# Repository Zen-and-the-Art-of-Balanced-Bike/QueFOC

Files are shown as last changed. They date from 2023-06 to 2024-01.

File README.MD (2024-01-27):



# QueFOC 无刷方案

- FOC有感无刷方案
- 已打板验证
- 已实现电流环、速度环
- 采用PLL算法观测速度
- 有完整的终端命令调试系统
- 提供完整的PCB工程文件（KICAD）

功率板
控制板
测试

## 文件目录介绍

```
PCB/ # 存放PCB KiCAD工程文件
  QueCtrl/ # 控制板的PCB工程文件
  QueDriverS/ # 功率板的PCB工程文件

QueFOC_dev/ # 电机控制程序

QueFOC_CH32V307/ # CH33V307单片机的工程目录
```

## 性能介绍

### 综合
使用此系统配合控制算法已实现K/N车平衡

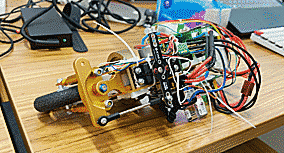
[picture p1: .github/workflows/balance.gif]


### 快速响应
使用逐飞的N车黑色无刷电机测试，280ms从0 turn/s达到50 turn/s



### 瞬间反转



## 移植说明

控制程序均采用函数指针加载，软硬完全解耦，移植仅需将`QueFOC_CH32V307`目录下的各函数按照单片机平台特性重新实现即可

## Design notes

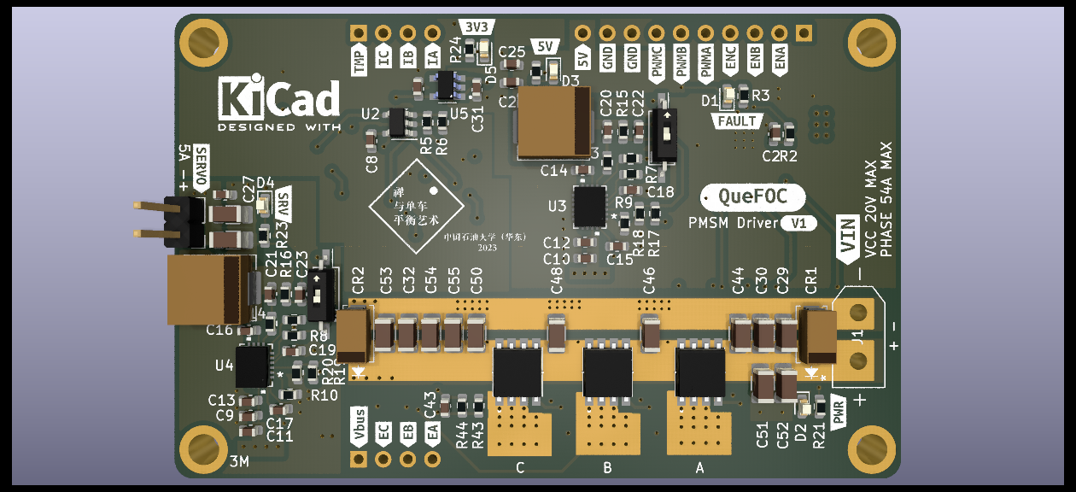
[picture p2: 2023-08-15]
PCB/QueDriverS/QueDriver.png

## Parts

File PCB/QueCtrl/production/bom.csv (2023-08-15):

Designator | Footprint | Quantity | Value | LCSC Part #
C1 | 0603 | 1 | 10uF
C10 | 0603 | 1 | 100nF
C11 | 0603 | 1 | 100nF
C12 | 0603 | 1 | 100nF
C13 | 0603 | 1 | 22uF
C14 | 0603 | 1 | 100nF
C16 | 0603 | 1 | 10nF
C17 | 0603 | 1 | 10nF
C18 | 0603 | 1 | 10nF
C2 | 0603 | 1 | 10uF
C3 | 0603 | 1 | 20pF
C4 | 0603 | 1 | 20pF
C5 | 0603 | 1 | 10uF
C6 | 0603 | 1 | 100nF
C7 | 0603 | 1 | 100nF
C8 | 0603 | 1 | 100nF
C9 | 0603 | 1 | 100nF
D1 | 0603 | 1 | LED
D2 | D_SOD-323 | 1 | 1N5819
D3 | 0603 | 1 | LED
D4 | 0603 | 1 | LED
F1 | 0603 | 1 | 500mA
J1 | PinHeader_1x07_P2.54mm_Horizontal | 1 | Conn_01x07
J10 | USB_C_Receptacle_HRO_TYPE-C-31-M-12 | 1 | USB_C_Receptacle_USB2.0
J11, J3, J4 | PinHeader_1x04_P2.54mm_Vertical | 3 | Conn_01x04
J2, J5 | JST_GH_SM06B-GHS-TB_1x06-1MP_P1.25mm_Horizontal | 2 | Conn_01x06
J6 | JST_PH_S4B-PH-SM4-TB_1x04-1MP_P2.00mm_Horizontal | 1 | Conn_01x04
J7 | PinHeader_1x10_P2.54mm_Vertical | 1 | Conn_01x10
J8 | PinSocket_1x04_P2.54mm_Horizontal | 1 | Conn_01x04
J9 | PinHeader_1x04_P2.54mm_Horizontal | 1 | Conn_01x04
R1 | 0603 | 1 | 10K
R10 | 0603 | 1 | 100R
R11 | 0603 | 1 | 100R
R12 | 0603 | 1 | 100R
R14 | 0603 | 1 | 4.7K
R15 | 0603 | 1 | 4.7K
R16 | 0603 | 1 | 4.7K
R2 | 0603 | 1 | 10K
R3 | 0603 | 1 | 10K
R4 | 0603 | 1 | 5.1K
R5 | 0603 | 1 | 5.1K
R7 | 0603 | 1 | 1K
R8 | 0603 | 1 | 1K
R9 | 0603 | 1 | 1K
SW1, SW2 | SW_SPST_CK_RS282G05A3 | 2 | SW_3*6*2.5
U1 | SOT94P279X129-5N | 1 | RT9013-33GB
U2 | LQFP-64_10x10mm_P0.5mm | 1 | CH32V305RBT6
U4 | TSSOP-20_4.4x6.5mm_P0.65mm | 1 | 74HC244
Y1 | Crystal_SMD_3225-4Pin_3.2x2.5mm | 1 | 8M

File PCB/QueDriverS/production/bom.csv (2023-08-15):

Designator | Footprint | Quantity | Value | LCSC Part #
C1 | 0603 | 1 | 100nF
C10 | 1206 | 1 | 10uF
C11 | 0603 | 1 | 10nF
C12 | 0603 | 1 | 10nF
C13, C14, C15 | CP_Elec_6.3x7.7 | 3 | 220uF
C16 | 0603 | 1 | 100nF
C17 | 0603 | 1 | 100nF
C2 | 0603 | 1 | 10uf
C29 | 1206 | 1 | 100uF
C3 | 0603 | 1 | 470nF
C30 | 1206 | 1 | 100uF
C31 | 0603 | 1 | 10uF
C32 | 1206 | 1 | 100uF
C33 | 0603 | 1 | 10uF
C34 | 0603 | 1 | 1nF
C35 | 0603 | 1 | 100nF
C36 | 0603 | 1 | 1nF
C37 | 0603 | 1 | 100nF
C38 | 0603 | 1 | 1nF
C39 | 0603 | 1 | 100nF
C4 | 0603 | 1 | 470nF
C40 | 0603 | 1 | 100nF
C41 | 0603 | 1 | 100nF
C42 | 0603 | 1 | 100nF
C43 | 0603 | 1 | 100nF
C44 | 1206 | 1 | 2.2uF
C45 | 0603 | 1 | 10nF
C46 | 1206 | 1 | 2.2uF
C47 | 0603 | 1 | 10nF
C48 | 1206 | 1 | 2.2uF
C49 | 0603 | 1 | 10nF
C5 | 0603 | 1 | 470nF
C50 | 1206 | 1 | 100uF
C51 | 1206 | 1 | 100uF
C52 | 1206 | 1 | 100uF
C53 | 1206 | 1 | 100uF
C54 | 1206 | 1 | 100uF
C55 | 1206 | 1 | 100uF
C56 | 1206 | 1 | 100uF
C6 | 0603 | 1 | 470nF
C7 | 0603 | 1 | 100nF
C8 | 0603 | 1 | 100nF
C9 | 1206 | 1 | 10uF
CR1, CR2, CR3, CR4, CR5 | SMAJ20CA-13-F | 5 | SMAJ20CA
D1 | 0603 | 1 | LED
D10, D11, D6, D7, D8, D9 | D_SOD-323 | 6 | 1N4148WS
D12 | 0603 | 1 | LED
D13, D14 | DO-214AC | 2 | B340A-13-F | B340A-13-F
D2 | 0603 | 1 | LED
D3 | 0603 | 1 | LED
D4 | 0603 | 1 | LED
D5 | 0603 | 1 | LED
J1 | AMASS_XT30UPB-M_1x02_P5.0mm_Vertical | 1 | XT30UPB-M
J2 | PinSocket_1x10_P2.54mm_Vertical | 1 | Conn_01x10
J3, J5 | PinSocket_1x04_P2.54mm_Vertical | 2 | Conn_01x04
J4 | PinHeader_1x02_P2.54mm_Vertical | 1 | Conn_01x02
L1, L2 | L_Abracon_ASPI-0630LR | 2 | 18uH
Q1, Q2, Q3, Q4, Q5, Q6 | TRANS_TPHR8504PL,L1Q | 6 | TPH1R403NL
R1 | 0603 | 1 | 200K
R2 | 0603 | 1 | 100K
R21 | 0603 | 1 | 10K
R22 | 0603 | 1 | 1K
R23 | 0603 | 1 | 1K
R24 | 0603 | 1 | 1K
R25 | 0603 | 1 | 1K
R26 | 0603 | 1 | 1K
R27 | 0603 | 1 | 30K
R28 | 0603 | 1 | 30K
R29 | 0603 | 1 | 1K
R3 | 0603 | 1 | 1K
R30 | 0603 | 1 | 1K
R31 | 0603 | 1 | 30K
R32 | 0603 | 1 | 30K
R33 | 0603 | 1 | 1K
R34 | 0603 | 1 | 1K
R35 | 0603 | 1 | 30K
R36 | 0603 | 1 | 30K
R37 | 0603 | 1 | 28K
R38 | 0603 | 1 | 2K
R39 | 0603 | 1 | 28K
R4 | 0603 | 1 | 10K
R40 | 0603 | 1 | 2K
R41 | 0603 | 1 | 28K
R42 | 0603 | 1 | 2K
R43 | 0603 | 1 | 28K
R44 | 0603 | 1 | 2K
R45 | 0603 | 1 | 33R
R46 | 0603 | 1 | 33R
R47 | 2512 | 1 | 1mR 3W
R48 | 0603 | 1 | 33R
R49 | 0603 | 1 | 33R
R5 | 0603 | 1 | 10K
R50 | 2512 | 1 | 1mR 3W
R51 | 0603 | 1 | 33R
R52 | 0603 | 1 | 33R
R53 | 2512 | 1 | 1mR 3W
R54 | 0603 | 1 | 1K
R6 | 0603 | 1 | 10K
R7 | 0603 | 1 | 10k
R8 | 0603 | 1 | 3.24k
R9 | 0603 | 1 | 10k
SW1 | 3386P | 1 | 10K
SW3 | SW_SPDT_MSK-12D19 | 1 | SW_SPDT
TH1 | 0805 | 1 | 10K
U1 | MP6530GR-Z | 1 | MP6530GR-Z
U2, U6, U7, U8 | SOT-23-5 | 4 | GS8551
U3, U4 | TI_SO-PowerPAD-8_ThermalVias | 2 | TPS5430DDA
U5 | SOT94P279X129-5N | 1 | RT9013-33GB

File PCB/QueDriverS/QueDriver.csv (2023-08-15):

Source: | S:\EE\PCB\Project\ZenAndArtOfBalanceBike\MotorDriver\QueDriver\QueDriver.kicad_sch
Date: | 2023/1/29 23:59:41
Tool: | Eeschema (6.0.7)
Generator: | S:\Program Files\KiCad\6.0\bin\scripting\plugins/bom_csv_grouped_by_value_with_rated_fp.py
Component Count: | 155
Ref | Qnty | Value | Cmp name | Footprint | Description | Vendor | Rated
C1, C7, C8, C12, C13, C14, C16, C18, C19, C20, C21, C25, C28, C35, C37, C39, C40, C41, C42, C43, | 20 | 100nF | C | Capacitor_SMD:C_0603_1608Metric | Unpolarized capacitor
C2, | 1 | 10uf | C | Capacitor_SMD:C_0603_1608Metric | Unpolarized capacitor |  | 16V
C3, C4, C5, C6, | 4 | 470nF | C | Capacitor_SMD:C_0603_1608Metric | Unpolarized capacitor |  | 35V
C9, C10, C11, | 3 | 4.7uF | C | Capacitor_SMD:C_0603_1608Metric | Unpolarized capacitor |  | 35V
C15, C17, | 2 | 1uF | C | Capacitor_SMD:C_0603_1608Metric | Unpolarized capacitor
C22, C23, | 2 | 3.9nF | C | Capacitor_SMD:C_0603_1608Metric | Unpolarized capacitor
C24, | 1 | 22uF | C | Capacitor_SMD:C_0603_1608Metric | Unpolarized capacitor
C26, C27, | 2 | 47uF | C | Capacitor_SMD:C_1206_3216Metric | Unpolarized capacitor
C29, C30, C32, C50, C51, C52, C53, C54, C55, C56, | 10 | 100uF | C | Capacitor_SMD:C_1206_3216Metric | Unpolarized capacitor |  | 50V
C31, C33, | 2 | 10uF | C | Capacitor_SMD:C_0603_1608Metric | Unpolarized capacitor
C34, C36, C38, | 3 | 1nF | C | Capacitor_SMD:C_0603_1608Metric | Unpolarized capacitor
C44, C46, C48, | 3 | 2.2uF | C | Capacitor_SMD:C_1206_3216Metric | Unpolarized capacitor |  | 50V
C45, C47, C49, | 3 | 10nF | C | Capacitor_SMD:C_0603_1608Metric | Unpolarized capacitor |  | 50V
CR1, CR2, CR3, CR4, CR5, | 5 | SMAJ20CA | SMAJ20CA | download-footprints:SMAJ20CA-13-F
D1, D2, D3, D4, D5, | 5 | LED | LED | LED_SMD:LED_0603_1608Metric | Light emitting diode
D6, D7, D8, D9, D10, D11, | 6 | 1N4148WS | 1N4148WS | Diode_SMD:D_SOD-323 | 75V 0.15A Fast switching Diode, SOD-323
J1, | 1 | XT30UPB-M | XT30U | Connector_AMASS:AMASS_XT30UPB-M_1x02_P5.0mm_Vertical
J2, | 1 | Conn_01x10 | Conn_01x10 | Connector_PinSocket_2.54mm:PinSocket_1x10_P2.54mm_Vertical | Generic connector, single row, 01x10, script generated (kicad-library-utils/schlib/autogen/connector/)
J3, J5, | 2 | Conn_01x04 | Conn_01x04 | Connector_PinSocket_2.54mm:PinSocket_1x04_P2.54mm_Vertical | Generic connector, single row, 01x04, script generated (kicad-library-utils/schlib/autogen/connector/)
J4, | 1 | Conn_01x02 | Conn_01x02 | Connector_PinHeader_2.54mm:PinHeader_1x02_P2.54mm_Vertical | Generic connector, single row, 01x02, script generated (kicad-library-utils/schlib/autogen/connector/)
L1, | 1 | 15.4uH | L | Inductor_SMD:L_Abracon_ASPI-0630LR | Inductor
L2, | 1 | 3.3uH | L | Inductor_SMD:L_Abracon_ASPI-0630LR | Inductor
Q1, Q2, Q3, Q4, Q5, Q6, | 6 | TPH1R403NL | Q_NMOS_DGS | download-footprints:TRANS_TPHR8504PL,L1Q | N-MOSFET transistor, drain/gate/source
R1, | 1 | 200K | R | Resistor_SMD:R_0603_1608Metric | Resistor
R2, R7, R8, R11, R12, | 5 | 100K | R | Resistor_SMD:R_0603_1608Metric | Resistor
R3, R22, R23, R24, R25, R26, R29, R30, R33, R34, | 10 | 1K | R | Resistor_SMD:R_0603_1608Metric | Resistor
R4, R5, R6, R21, R54, R55, R56, R57, R58, R59, | 10 | 10K | R | Resistor_SMD:R_0603_1608Metric | Resistor
R9, | 1 | 101.54k | R | Resistor_SMD:R_0603_1608Metric | Resistor
R10, | 1 | 151.54K | R | Resistor_SMD:R_0603_1608Metric | Resistor
R13, R14, | 2 | 4.7R | R | Resistor_SMD:R_0603_1608Metric | Resistor
R15, R16, | 2 | 95.3K | R | Resistor_SMD:R_0603_1608Metric | Resistor
R17, R19, | 2 | 97.6K | R | Resistor_SMD:R_0603_1608Metric | Resistor
R18, | 1 | 9.53K | R | Resistor_SMD:R_0603_1608Metric | Resistor
R20, | 1 | 6.04K | R | Resistor_SMD:R_0603_1608Metric | Resistor
R27, R28, R31, R32, R35, R36, | 6 | 30K | R | Resistor_SMD:R_0603_1608Metric | Resistor
R37, R39, R41, R43, | 4 | 28K | R | Resistor_SMD:R_0603_1608Metric | Resistor
R38, R40, R42, R44, | 4 | 2K | R | Resistor_SMD:R_0603_1608Metric | Resistor
R45, R46, R48, R49, R51, R52, | 6 | 33R | R | Resistor_SMD:R_0603_1608Metric | Resistor
R47, R50, R53, | 3 | 1mR 3W | R | Resistor_SMD:R_2512_6332Metric | Resistor
SW1, SW2, | 2 | SW_SPST | SW_SPST | Button_Switch_SMD:SW_DIP_SPSTx01_Slide_Copal_CHS-01B_W7.62mm_P1.27mm | Single Pole Single Throw (SPST) switch
TH1, | 1 | 10K | Thermistor_NTC | Resistor_SMD:R_0603_1608Metric | Temperature dependent resistor, negative temperature coefficient
U1, | 1 | MP6530GR-Z | MP6530GR-Z | download-footprints:MP6530GR-Z
U2, U6, U7, U8, | 4 | GS8551 | GS8551 | Package_TO_SOT_SMD:SOT-23-5
U3, U4, | 2 | MP4470 | MP4470 | download-footprints:MP4470
U5, | 1 | RT9013-33GB | RT9013-33GB | download-footprints:SOT94P279X129-5N

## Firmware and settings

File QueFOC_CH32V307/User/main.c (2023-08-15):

#include "motor.h"
#include "hardware.h"
#include "foc.h"
#include "fast_math.h"
#include "oled.h"

Motor motorQ={0};
Encoder encoderQ={0};
ADC_sensor adcQ={0};
PWM pwmQ={0};

Cmder cmder={0};
Monitor monitor={0};


void hardware_basic_boot(){
    hardware_motor_gpio_boot();
    hardware_nvic_boot();
    hardware_dma_boot();
}

void hardware_encoder_boot(){
    hardware_encoder_gpio_boot();
    hardware_encoder_spi_boot();
}

void hardware_uart4_callback(float data){
	if(data<100&&data>-100)
    	motorQ.vel_input = data;
    //monitor_prt(&monitor, "cmd.vel=%.7f\n", data);
}


int main(void)
{
	//USART_Printf_Init(115200);
    hardware_delay_init();

#if USE_USB_CDC
    monitor_init(&monitor,
            hardware_usb_fs_cdc_boot, hardware_usb_cdc_send);
#else
    monitor_init(&monitor,
            hardware_usart3_boot, hardware_usart3_send_str);
#endif
    monitor_boot(&monitor);
    monitor_prt(&monitor, "SystemClk:%d\r\n", SystemCoreClock);

    encoder_init(&encoderQ, PWM_FREQUENCY, CPR, POLE_PAIRS, hardware_encoder_boot, hardware_encoder_spi_data);

	adc_sensor_init(&adcQ,
	        PWM_FREQUENCY, ADC_RESOLUTION_BIT,
	        I_OP_AMP_GAIN, I_OP_AMP_OFFSET, V_BUS_GAIN, SHUNT_RESISTANCE,
	        hardware_adc_boot,
	        hardware_adc_read_phase_a, hardware_adc_read_phase_b, hardware_adc_read_phase_c,
	        hardware_adc_read_vbus, hardware_adc_read_vgnd);
	pwm_init(&pwmQ,
	        PWM_FREQUENCY,
	        hardware_pwm_boot,
	        hardware_set_pwm_duty_ch_a, hardware_set_pwm_duty_ch_b, hardware_set_pwm_duty_ch_c);
	cmder_init(&cmder,
	        '\n', false,
	        hardware_usart3_boot, hardware_usart3_send_str);
	motor_init(&motorQ,
	        'Q', KV, CALIB_CURRENT, CALIB_VOLTAGE,
	        PWM_FREQUENCY*0.1, INERTIA,
	        2, 5, 12, 28,
	        100, I_MAX,
	        &encoderQ, &adcQ, &pwmQ, &cmder,
	        hardware_basic_boot);



	cmder_boot(&cmder);

	hardware_delay_ms(500);

	//encoder_boot(&encoderQ);

	motor_boot(&motorQ);

	cmder_add_motor(&cmder, &motorQ);

	//hardware_encoder_IIF_boot();


	monitor_prt(&monitor, "SystemClk:%d\nv_bus=%f", SystemCoreClock, motorQ.adc->v_bus);

	hardware_delay_ms(500);

	/* LED Blink */
	RCC_APB2PeriphClockCmd( RCC_APB2Periph_GPIOC , ENABLE );
	GPIO_InitTypeDef GPIO_InitStructure={0};
	GPIO_InitStructure.GPIO_Pin = GPIO_Pin_12;
    GPIO_InitStructure.GPIO_Mode = GPIO_Mode_Out_PP;
    GPIO_InitStructure.GPIO_Speed = GPIO_Speed_2MHz;
    GPIO_Init(GPIOC, &GPIO_InitStructure);
    GPIO_SetBits(GPIOB, GPIO_Pin_12);

    GPIO_SetBits(GPIOC, GPIO_Pin_3 | GPIO_Pin_4 | GPIO_Pin_5);
    //GPIO_ResetBits(GPIOB, GPIO_Pin_12);

    // 0.1 0.01 FOR BETTER VEL CTRL PERFORMANCE
    motor_update_vel_ctrl_param(&motorQ, 0.05, 0.001);
    hardware_uart4_boot();

//    OLED_Init();
//    OLED_Clear();
//    OLED_ShowChar(10,20,'B',16);
//    monitor_prt(&monitor, "OLED INIT\n");

//
//    while(1){
//        trans_data_package_float(1.23456f, hardware_uart4_send_u8);
//        hardware_delay_ms(5);
//        trans_data_package_float(6.54321f, hardware_uart4_send_u8);
//        hardware_delay_ms(5);
//    }


	while(1){


//	    led ^= 1; b
//	    if(led)
//	        GPIO_ResetBits(GPIOC, GPIO_Pin_12);
//	    else
//	        GPIO_SetBits(GPIOC, GPIO_Pin_12);
//
//	    monitor_prt(&monitor, "%d\n", motorQ.state);
	    if(motorQ.state == MS_RUN_VELOCITY){
	        GPIO_SetBits(GPIOC, GPIO_Pin_12);
	        trans_data_package_float(motorQ.encoder->vel, hardware_uart4_send_u8);

			// Faster
	        hardware_delay_ms(1);

//	        monitor_prt(&monitor, "%d %.3f %.3f %.3f\n", encoderQ.data_raw, (encoderQ.data_raw-encoderQ.offset)*1.0f*PIx2*7/16384, encoderQ.phase, encoderQ.phase*360/PIx2);


//	        if(foc_voltage_control(&motorQ, 0, 1, (encoderQ.data_raw-encoderQ.offset)*1.0f*PIx2*7/16384))
//	            pwm_sync_duty(motorQ.pwm);
//	        if(foc_voltage_control(&motorQ, 0, 1, encoderQ.phase))
//	            pwm_sync_duty(motorQ.pwm);
//	        monitor_prt(&monitor, "%.3f %.3f\n", encoderQ.phase, (encoderQ.data_raw-encoderQ.offset)*PIx2*7/16384);

//	        monitor_prt(&monitor, "%.3f,%.3f,%.3f,%.3f\n", motorQ.i_d, 0.0f, motorQ.i_q, motorQ.i_q_set);
//	        monitor_prt(&monitor, "%.3f,%.3f\n", motorQ.vel_sp, motorQ.encoder->vel);



//	        monitor_prt(&monitor, "%.3f,%.3f,%.3f,%.3f\n", motorQ.i_q, debug_id_set, motorQ.encoder->vel, motorQ.encoder->pos);
//	        monitor_prt(&monitor, "%.3f,%.3f\n", motorQ.encoder->vel, motorQ.i_q_set);
//	         monitor_prt(&monitor, "%.3f,%.3f,%.3f,%.3f,%.3f\n", motorQ.i_q, motorQ.i_q_set, motorQ.encoder->vel, motorQ.vel_input, motorQ.ctrl_vel_integral);
//			 hardware_delay_ms(5);


	    }else {

	        GPIO_ResetBits(GPIOC, GPIO_Pin_12);
        }



	}

}

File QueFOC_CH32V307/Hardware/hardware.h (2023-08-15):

/*
 * hardware.h
 *
 *  Created on: Dec 31, 2022
 *      Author: 24216
 */

#ifndef HARDWARE_HARDWARE_H_
#define HARDWARE_HARDWARE_H_

#include "ch32v30x.h"

#define bool            int
#define false           0
#define true            1

#define USE_USB_CDC                 0

/* SYSTEM */
#define PWM_FREQUENCY               20000


/* ADC */
/* ADC_CLK = PCLK2 / ADC_CLK_DIV
 * Note that CH32V30x ADCCLLK < 14 MHz
 */
#define ADC_CLK_DIV RCC_PCLK2_Div6
//#define ADC_CLK_DIV RCC_PCLK2_Div8
// FIXME
// SAMPLE_TIME_CLK + 12.5 * ADC_CLK
// 14 * (1/12)MHz = 1.16us
#define ADC_SAMPLE_TIME             ADC_SampleTime_7Cycles5
#define ADC_TRIGGER                 ADC_ExternalTrigInjecConv_Ext_IT15_TIM8_CC4

/* TIM */
/* PWM */
#define TIM_PWM                     TIM8
#define TIM_PWM_RCC                 RCC_APB2Periph_TIM8
#define TIM_PWM_CLK                 SystemCoreClock
#define PWM_PERIOD_CYCLES           (uint16_t)((TIM_PWM_CLK/((uint32_t)(PWM_FREQUENCY)))&0xFFFE)
#define HALF_PWM_PERIOD_CYCLES      (uint16_t)(PWM_PERIOD_CYCLES/2U)
#define TIM_ADC_SAMPLE_TIMING       5
/* IIF(ABZ) */
#define TIM_IIF                     TIM4
#define TIM_IIF_RCC                 RCC_APB1Periph_TIM4


/* User configuration */
#define KV                          400
#define POLE_PAIRS                  7
#define INERTIA                     0
#define CPR                         (1<<14)
#define ADC_RESOLUTION_BIT          12
#define V_BUS_GAIN                  15
#define SHUNT_RESISTANCE            0.001f
#define I_OP_AMP_OFFSET             1.65f
#define I_OP_AMP_GAIN               30.0f
#define CALIB_CURRENT               2.0f
#define CALIB_VOLTAGE               1.0f
#define I_MAX                       15.0f
// FIXME
// IR2136 290ns
#define DEAD_TIME_NS                0
#define PWM_DEADTIME                (int)(DEAD_TIME_NS/(1.0f*1000/(TIM_PWM_CLK/1000000)))

#define ENCODER_SPIx                SPI2
#define ENCODER_SPI_RCC             RCC_APB1Periph_SPI2



/* GPIO */
void hardware_motor_gpio_boot();
void hardware_encoder_gpio_boot();

/* NVIC */
void hardware_nvic_boot();

/* DMA */
void hardware_dma_boot();

/* DELAY */
void hardware_delay_init(void);
void hardware_delay_us(uint32_t n);
void hardware_delay_ms(uint32_t n);

/* ADC */
void hardware_adc_boot();
u16 hardware_adc_read_phase_a();
u16 hardware_adc_read_phase_b();
u16 hardware_adc_read_phase_c();
u16 hardware_adc_read_vbus(void);
u16 hardware_adc_read_vgnd(void);

/* PWM */
void hardware_pwm_boot(void);
void hardware_set_pwm_duty_ch_a(float duty);
void hardware_set_pwm_duty_ch_b(float duty);
void hardware_set_pwm_duty_ch_c(float duty);

/* USART */
void hardware_usart3_boot(void);
void hardware_usart3_send_str(const char* data);

void trans_data_package_float(const float data, void (*send)(uint8_t));
void rec_data_package_float(const uint8_t rec, void (*callback)(float));

void hardware_uart4_boot(void);
void hardware_uart4_send_u8(const u8 data);
void hardware_uart4_callback(float data);

/* USB */
void hardware_usb_fs_cdc_boot(void);
void hardware_usb_cdc_send(const char* data);

/* IIF(ABZ) */
void hardware_encoder_IIF_boot(void);
uint16_t hardware_encoder_IIF_query(void);

/* SPI */
void hardware_encoder_spi_boot();
bool hardware_encoder_spi_data(u16 *data);

#endif /* HARDWARE_HARDWARE_H_ */

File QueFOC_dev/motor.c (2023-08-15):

//
// Created by 24216 on 2022/12/23.
//

#include "motor.h"
#include "foc.h"
#include <string.h>

extern Monitor monitor;

void motor_init(Motor* motor,
                uint8_t id, uint32_t KV, float calib_current, float calib_voltage,
                float ctrl_i_bandwidth, float inertia,
                float limit_i_bus_max, float limit_i_leak_max, float limit_v_bus_min, float limit_v_bus_max,
                float limit_vel_max, float limit_i_max,
                Encoder* encoder, ADC_sensor* adc, PWM* pwm, Cmder* cmder,
                void (*hardware_basic_boot)(void)){
    // clean up
    memset(motor, 0, sizeof(Motor));

    motor->id = id;
    motor->calib_current = calib_current;
    motor->calib_voltage = calib_voltage;
    motor->i_ctrl_bandwidth = ctrl_i_bandwidth;
    motor->inertia = inertia;

    motor->limit_i_bus_max = limit_i_bus_max;
    motor->limit_i_leak_max = limit_i_leak_max;
    motor->limit_v_bus_min = limit_v_bus_min;
    motor->limit_v_bus_max = limit_v_bus_max;
    motor->limit_vel_max = limit_vel_max;
    motor->limit_i_max = limit_i_max;


    motor->encoder = encoder;
    motor->adc = adc;
    motor->pwm = pwm;
    motor->cmder = cmder;
    motor->hardware_basic_boot = hardware_basic_boot;

    // A approximation for torque constant (Nm/A) from Odrive
    motor->torque_constant = 8.27f / (float)(KV);


    motor->state = MS_CREATED;
}

void motor_boot(Motor* motor){
    motor->hardware_basic_boot();
    // FIXME
    encoder_boot(motor->encoder);
    adc_boot(motor->adc);
    pwm_boot(motor->pwm);

    motor->state = MS_BOOTED;
}

void motor_stop(Motor* motor){
    foc_refresh(motor);
    pwm_apply_duty(motor->pwm, 0, 0, 0);
}

void motor_shift_state(Motor* motor, Motor_state state){
    motor->state = state;
}

void interrupt_adc_done(Motor* motor){
    motor_loop_main(motor);
}


void motor_loop_main(Motor* motor){
    adc_update(motor->adc);
    foc_update_d_q(motor);
    // FIXME
    if(!encoder_update(motor->encoder)){
        motor->state = MS_ERROR_ENCODER_COMMUNITE_FAIL;
    }


    if(IF_CONTAIN_IN(motor->state, MS_RUN_BEGIN, MS_RUN_END))
        motor_loop_run(motor);
    else if(IF_CONTAIN_IN(motor->state, MS_CALIBRATION_BEGIN, MS_CALIBRATION_END-1))
        motor_loop_calibration(motor);
    else if(IF_CONTAIN_IN(motor->state, MS_ERROR_BEGIN, MS_ERROR_END))
        motor_loop_error(motor);
    else if(motor->state == MS_BOOTED)
        motor->state = MS_CALIBRATION_BEGIN;
    else if(motor->state == MS_CALIBRATION_END)
        // When everything is ready, where to go?
        motor->state = MS_RUN_VELOCITY;
//        motor->state = MS_TEST;
    else if(motor->state == MS_TEST){

//        monitor_prt(&monitor, "%.3f,%.3f\n",
//                //(float)motor->encoder->cnt_raw - (float)motor->encoder->offset,
//                fmodf_real(motor->encoder->i_phase, PIx2),
////                  fmodf_real(0, PIx2)
//                motor->encoder->data_raw
//                );
//        static float pha_set = 0;
//        monitor_prt(&monitor, "%f,%f,%f,%f\n",
//                    //(float)motor->encoder->cnt_raw - (float)motor->encoder->offset,
//                motor->encoder->i_phase, pha_set,
//                        fmodf_real(motor->encoder->i_phase, PIx2),
//                                  fmodf_real(pha_set, PIx2)
//        //            motorQ.encoder->offset
//                    );
//        pha_set += PI/10;
//        if(foc_voltage_control(motor, 1, 0, pha_set))
//            pwm_sync_duty(motor->pwm);
//        hardware_delay_ms(1000);

//
//        monitor_prt(&monitor, "%d\n",
//            //(float)motor->encoder->cnt_raw - (float)motor->encoder->offset,
//                motor->encoder->data_raw
////            motorQ.encoder->offset
//            );



//        if(foc_voltage_control(motor, 0, 5, motor->encoder->i_phase))
//            pwm_sync_duty(motor->pwm);

//          if(foc_voltage_control(motor, 0.5, 0, 0))
//              pwm_sync_duty(motor->pwm);
//          monitor_prt(&monitor, "%.3f,%.3f,%.3f\n", motor->adc->i_a, motor->adc->i_b, motor->adc->i_c);
//          monitor_prt(&monitor, "%d\n", motor->encoder->data_raw);
//          hardware_delay_ms(10);
        if(foc_current_control(motor, 0, 0.5, motor->encoder->i_phase, motor->encoder->i_phase))
            pwm_sync_duty(motor->pwm);

//        if(foc_d_q_vec_control(motor, 0.2, PI_2, motor->encoder->phase))
//            pwm_sync_duty(motor->pwm);

    }
    else if(motor->state == MS_IDLE || motor->state == MS_CREATED)
        return;
    else
        motor->state = MS_ERROR_UNKNOWN_STATE;
}

void motor_loop_calibration(Motor* motor){
    static uint32_t step_loop_cnt = 0;
    static float voltages[3] = {0};
    static float currents_f[3] = {0};
    static uint32_t currents[3] = {0};
    uint32_t phase_resistance_loop_cnt = 3*motor->adc->measure_freq;
    uint32_t phase_inductance_loop_cnt = motor->adc->measure_freq/2;
    static float cur_phase = 0;

    // current step loop cnt
    step_loop_cnt += 1;

    switch (motor->state) {
        case MS_CALIBRATION_BEGIN:
        {
            motor->state = MS_CALIBRATION_PHASE_CURRENT_OFFSET_INIT;
        }
            break;
        /* phase current OP-AMP offset  */
        case MS_CALIBRATION_PHASE_CURRENT_OFFSET_INIT:
        {
            // set phase current to zero
            pwm_apply_duty(motor->pwm, 0, 0, 0);
            step_loop_cnt = 0;
            currents[0] = currents[1] = currents[2] = 0;
            motor->state = MS_CALIBRATION_PHASE_CURRENT_OFFSET_LOOP;
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

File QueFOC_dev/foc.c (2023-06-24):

//
// Created by 24216 on 2022/12/21.
//

#include "foc.h"
#include "fast_math.h"
#include "math.h"

//float DEBUG_ALPHA, DEBUG_BETA;

void foc_refresh(Motor* motor){
    motor->torque_sp = motor->vel_sp = 0;
    motor->ctrl_i_integral_id = motor->ctrl_i_integral_iq = 0;
    motor->i_d = motor->i_q = 0;
}

static bool foc_d_q_mod_control(Motor* motor, float mod_d, float mod_q, float phase){
    // Inverse park transform
    float mod_alpha, mod_beta;
    inverse_park(mod_d, mod_q, phase, &mod_alpha, &mod_beta);

//    DEBUG_ALPHA = mod_alpha;
//    DEBUG_BETA = mod_beta;

    // SVM
    if(!foc_modulation_svm(mod_alpha, mod_beta, &(motor->pwm->duty_a), &(motor->pwm->duty_b), &(motor->pwm->duty_c))){
        motor->state = MS_ERROR_SVM_RESULT_INVALID;
        return false;
    }
    return true;
}

bool foc_d_q_vec_control(Motor* motor, float vec_len, float vec_angle, float phase){
    if(ABS(vec_len) > 1) return false;
    vec_len = vec_len * SQRT3_BY_2;
    float mod_d = vec_len * fast_cos(vec_angle);
    float mod_q = vec_len * fast_sin(vec_angle);

    return foc_d_q_mod_control(motor, mod_d, mod_q, phase);
}

bool foc_alpha_beta_vec_control(Motor* motor, float vec_len, float vec_angle){
    return foc_d_q_vec_control(motor, vec_len, vec_angle, 0);
}

void foc_update_d_q(Motor* motor){
    // Clarke transform
    clarke_transform(motor->adc->i_a, motor->adc->i_b, motor->adc->i_c, &motor->i_alpha, &motor->i_beta);

    // Park transform
    park_transform(motor->i_alpha, motor->i_beta, motor->encoder->i_phase, &motor->i_d, &motor->i_q);
}

bool foc_voltage_control(Motor* motor, float Vd_set, float Vq_set, float phase)
{

    // Modulation
    float V_to_mod = 1.0f / VBUS_TO_VPHASE_MAX(motor->adc->v_bus);
    float mod_d = V_to_mod * Vd_set;
    float mod_q = V_to_mod * Vq_set;

    // Vector modulation saturation
    float mod_scalefactor = MAX_MODULATION_SCALE * SQRT3_BY_2 / fast_sqrt(SQ(mod_d) + SQ(mod_q));
    if (mod_scalefactor < 1.0f) {
        mod_d *= mod_scalefactor;
        mod_q *= mod_scalefactor;
    }

    return foc_d_q_mod_control(motor, mod_d, mod_q, phase);
}

bool foc_current_control(Motor* motor, float Id_set, float Iq_set, float I_phase, float PWM_phase)
{


    float mod_to_V = VBUS_TO_VPHASE_MAX(motor->adc->v_bus);
    float V_to_mod = 1.0f / mod_to_V;

    // Apply PI control
    float Ierr_d = Id_set - motor->i_d;
    float Ierr_q = Iq_set - motor->i_q;
    float mod_d = V_to_mod * (motor->ctrl_i_integral_id + Ierr_d * motor->ctrl_i_kp);
    float mod_q = V_to_mod * (motor->ctrl_i_integral_iq + Ierr_q * motor->ctrl_i_kp);

    // Vector modulation saturation, lock integrator if saturated
    float mod_scalefactor = MAX_MODULATION_SCALE * SQRT3_BY_2 / fast_sqrt(SQ(mod_d) + SQ(mod_q));
    if (mod_scalefactor < 1.0f) {
        mod_d *= mod_scalefactor;
        mod_q *= mod_scalefactor;
        motor->ctrl_i_integral_id *= 0.99f;
        motor->ctrl_i_integral_iq *= 0.99f;
    } else {
        motor->ctrl_i_integral_id += Ierr_d * motor->ctrl_i_ki * motor->adc->measure_period;
        motor->ctrl_i_integral_iq += Ierr_q * motor->ctrl_i_ki * motor->adc->measure_period;
    }

    motor->adc->i_bus = (mod_d*motor->i_d + mod_q*motor->i_q);

    return foc_d_q_mod_control(motor, mod_d, mod_q, PWM_phase);
}

void clarke_transform(float a, float b, float c, float *alpha, float *beta)
{
    *alpha = a;
    *beta  = (b - c) * ONE_BY_SQRT3;
}

void park_transform(float alpha, float beta, float theta, float *d, float *q)
{
    float s = fast_sin(theta);
    float c = fast_cos(theta);
    *d =   alpha * c + beta * s;
    *q = - alpha * s + beta * c;
}

void inverse_park(float d, float q, float theta, float *alpha, float *beta)
{
    float s = fast_sin(theta);
    float c = fast_cos(theta);
    *alpha = d * c - q * s;
    *beta  = d * s + q * c;
}

/*!
 * @brief calculate the pwm duty by alpha and beta
 * @note the sign of alpha and beta depends on current direction,
 * here the positive direction is defined as the direction from the positive DC link to the negative DC link,
 * rather than defining the direction of flow into the motor winding as the positive direction
 * @param[in]   alpha alpha
 * @param[in]   beta beta
 * @param[out]  tA pwm duty of channel A
 * @param[out]  tB pwm duty of channel B
 * @param[out]  tC pwm duty of channel C
 * @retval  return 0 if result invalid
*/
bool foc_modulation_svm(float alpha, float beta, float* tA, float* tB, float* tC)
{
    int Sextant;

    if (beta >= 0.0f) {
        if (alpha >= 0.0f) {
            //quadrant I
            if (ONE_BY_SQRT3 * beta > alpha)
                Sextant = 2; //sextant v2-v3
            else
                Sextant = 1; //sextant v1-v2

        } else {
            //quadrant II
            if (-ONE_BY_SQRT3 * beta > alpha)
                Sextant = 3; //sextant v3-v4
            else
                Sextant = 2; //sextant v2-v3
        }
    } else {
        if (alpha >= 0.0f) {
            //quadrant IV
            if (-ONE_BY_SQRT3 * beta > alpha)
                Sextant = 5; //sextant v5-v6
            else
                Sextant = 6; //sextant v6-v1
        } else {
            //quadrant III
            if (ONE_BY_SQRT3 * beta > alpha)
                Sextant = 4; //sextant v4-v5
            else
                Sextant = 5; //sextant v5-v6
        }
    }

    switch (Sextant) {
        // sextant v1-v2
        case 1: {
            // Vector on-times
            float t1 = alpha - ONE_BY_SQRT3 * beta;
            float t2 = TWO_BY_SQRT3 * beta;

            // PWM timings
            *tA = (1.0f - t1 - t2) * 0.5f;
            *tB = *tA + t1;
            *tC = *tB + t2;
        } break;

        // sextant v2-v3
        case 2: {
            // Vector on-times
            float t2 = alpha + ONE_BY_SQRT3 * beta;
            float t3 = -alpha + ONE_BY_SQRT3 * beta;

            // PWM timings
            *tB = (1.0f - t2 - t3) * 0.5f;
            *tA = *tB + t3;
            *tC = *tA + t2;
        } break;

        // sextant v3-v4
        case 3: {
            // Vector on-times
            float t3 = TWO_BY_SQRT3 * beta;
            float t4 = -alpha - ONE_BY_SQRT3 * beta;

            // PWM timings
            *tB = (1.0f - t3 - t4) * 0.5f;
            *tC = *tB + t3;
            *tA = *tC + t4;
        } break;

        // sextant v4-v5
        case 4: {
            // Vector on-times
            float t4 = -alpha + ONE_BY_SQRT3 * beta;
            float t5 = -TWO_BY_SQRT3 * beta;

            // PWM timings
            *tC = (1.0f - t4 - t5) * 0.5f;
            *tB = *tC + t5;
            *tA = *tB + t4;
        } break;

        // sextant v5-v6
        case 5: {
            // Vector on-times
            float t5 = -alpha - ONE_BY_SQRT3 * beta;
            float t6 = alpha - ONE_BY_SQRT3 * beta;

            // PWM timings
            *tC = (1.0f - t5 - t6) * 0.5f;
            *tA = *tC + t5;
            *tB = *tA + t6;
        } break;
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

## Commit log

2023-06-24 first commit 测试
2023-07-01 fix uart protocol
2023-07-01 fix protocol again QAQ, ctrl with uart test passed
    [main.c, usart.c]
2023-08-15 fully open source; add PCB
2023-08-15 full open source include PCB
    [CAN.kicad_sch, Connector.kicad_sch, Current Sensor.kicad_sch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]
